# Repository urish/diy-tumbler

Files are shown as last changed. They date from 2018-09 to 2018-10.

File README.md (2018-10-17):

Do-It-Yourself Rock Tumbler
===========================

A simple Rock Tumbler I built from scratch in just a few hours.

For more information read the blog post: [Improvising Hardware: DiY Rotary Rock Tumbler](https://medium.com/@urish/improvising-hardware-diy-rotary-rock-tumbler-d3a1a1915ea9)

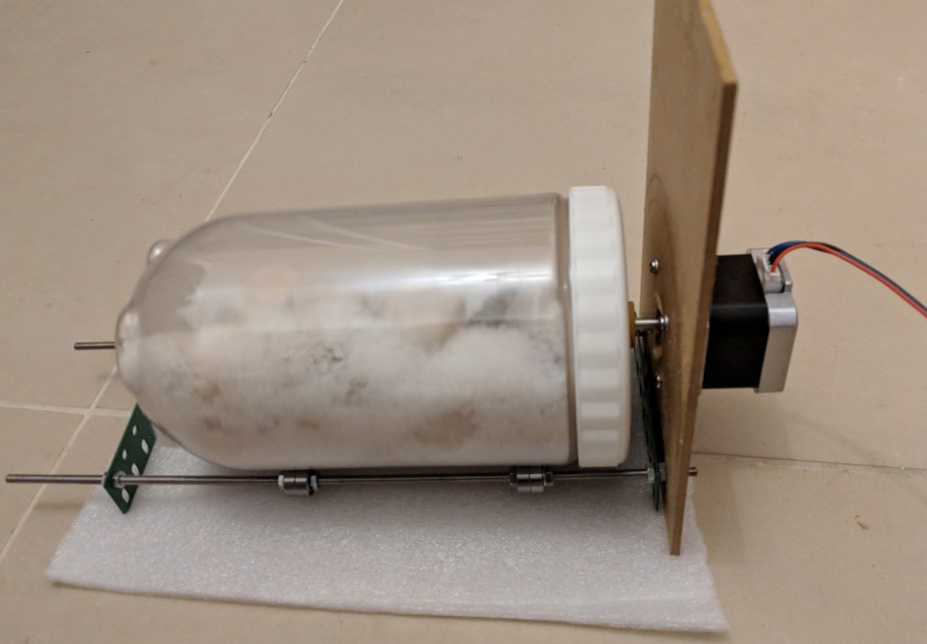
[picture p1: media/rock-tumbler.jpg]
DiY Rock Tumbler


## Bill of Materials

| Name | Quantity | Unit Price | Link | Comment |
|---| ---| --- | ---- | --- |
| Bipolar 1.7A 2.8V NEMA-17 Stepper Motor | 1 | $16.95 | [Pololu](https://www.pololu.com/product/2267) or [AliExpress](https://www.aliexpress.com/item/CE-certification-1pcs-4-lead-Nema17-Stepper-Motor-42-motor-Nema-17-motor-42BYGH-1-7A/32760823826.html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 )| |
| DRV8825 Motor Driver | 1 | $8.95 | [Pololu](https://www.pololu.com/product/2133) or [AliExpress](https://www.aliexpress.com/item/5pcs-lot-3D-Printer-Stepstick-Drv8825-Stepper-Motor-Driver-Reprap-4-PCB-Board-Free-shipping/32434801528.html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) |  |
| Pixl.js Espruino Board | 1 | $44.95 | [Espruino](https://shop.espruino.com/pixljs) or [AdaFruit](https://www.adafruit.com/product/3855) |  |
| KY-003 Hall Magnetic Sensor Module | 1 | $0.82 | [AliExpress](https://www.aliexpress.com/item/KY-003-Standard-Hall-Magnetic-Sensor-Module-Works-with-Arduino-Boards-for-Arduino/32693432353.html) | |
| A small magnet | 1 | | | |
| 28.8cm M4 Threaded Rod | 2 | - | | Different length possible |
| M4 Nut | 18 |  |  |  |
| M3x10 Screw | 12 | | | | 
| M3x8 Screw | 1 | | | |
| M3 Nut | 9 | | | |
| M3 Washer | 16 | | | |
| M2x16 Screw | 2 | | | |
| M2 Nut | 6 | | | |
| 624ZZ Bearing | 8 |  |  |  |
| Small Plastic Jar | 1 | | | |
| Small Plywood Board | 1 | | | |

You can replace the Pixl.js with a Arduino, though the built-in display make it really nice.

You also need to print 1 of each of these parts:
* [motor-mount.scad](hardware/parts/motor-mount.scad)
* [motor-hub.scad](hardware/parts/motor-hub.scad) - You may need to change the `diameter` variable to match the inner diameter of your Jar's cap (it can also be smaller)

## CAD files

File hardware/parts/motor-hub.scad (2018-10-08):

// Tumbling Machine - Motor Hub
// Copyright (C) 2018, Uri Shaked
// License: MIT

include <MCAD/units.scad>
use <../vitamins/nuts.scad>

diameter = 80;
totalHeight = 20;
hubHeight = 15;
hubDiameter = 22.5;
screwHeight = totalHeight - 5;
tolerance = 0.15;

$fn = 60;

module MotorHub() {
    difference() {
        union() {
            cylinder(h=totalHeight - hubHeight, r=diameter / 2);

            translate([0, 0, totalHeight - hubHeight])
            cylinder(r=hubDiameter / 2, h=hubHeight);
        }

        // motor shaft hole
        translate([0, 0, -epsilon])
        difference() {
            cylinder(r=2.5 + tolerance, h=totalHeight + 2*epsilon);

            translate([2.35 + tolerance, -5, 0])
            cube([10, 10, totalHeight+epsilon]);
        }

        // mounting holes
        for (angle = [0:360 / 8:360])
            rotate([0, 0, angle])
            translate([0, 30, 0])
            cylinder(r=M3 / 2 + tolerance, h=5 + epsilon);

        translate([0, 0, screwHeight]) {
            rotate([0, 90, 0])
            cylinder(h=hubDiameter/2 + epsilon, r = M3 / 2 + tolerance);

            translate([M3 / 2 + 3, 0, 0])
            rotate([90, 0, 90])
            NutM3Hole(2.4);
        }
    }
}

MotorHub();

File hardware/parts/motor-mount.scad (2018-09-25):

// Tumbling Machine - Motor Hub
// Copyright (C) 2018, Uri Shaked
// License: MIT

include <MCAD/units.scad>

$fn = 60;

mountWidth = 1.725 * inch;
mountThickness = 3;
pilotRadius = 0.433 * inch;
mountHoleDistance = 1.220 * inch;
mountHoleRadius = 1.5;
tolerance = 0.15;

module Nema17Mount() {
    difference() {
        translate([-mountWidth / 2, -mountWidth / 2, 0])
        cube([mountWidth, mountWidth, mountThickness]);

        translate([0,0,-0.05])
        cylinder(r=pilotRadius+tolerance, h=mountThickness + 0.1);

        // Motor mounting holes
        for (x=[0,1]) for (y=[0,1])
            mirror([x,y,0])
            translate([mountHoleDistance / 2, mountHoleDistance / 2,-0.05])
            cylinder(r=mountHoleRadius + tolerance,h = mountThickness + 0.1);
    }
}

Nema17Mount();

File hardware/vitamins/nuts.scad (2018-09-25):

include <MCAD/units.scad>
include <MCAD/materials.scad>

NutM3Radius = 3.2;

module NutM3(height = 2.4, tolerance = 0) {
    color(Steel)
    difference() {
        cylinder(h=height, r=NutM3Radius + tolerance, $fn = 6);

        translate([0, 0, -epsilon/2])
        cylinder(h=height+epsilon, r=1.5 + tolerance, $fn = 60);
    }
}

module NutM3Hole(height = 2.4, tolerance = 0.15, trap = true) {
    cylinder(h=height + tolerance, r=NutM3Radius + tolerance, $fn = 6);

    if (trap) {
        translate([-(NutM3Radius + tolerance), 0, 0])
        cube([(NutM3Radius + tolerance) * 2, (NutM3Radius + tolerance) * 2, height + tolerance]);
    }
}

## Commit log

2018-09-25 Improve motor hub
    [motor-hub.scad]
2018-09-25 docs: add BOM
2018-09-28 feat: add hall-effect revolution sensor
    - count and display revolutions
    - attempt slowing down and recovering if we detect loss of motion
2018-10-08 fix(hardware): make the motor hub thicker and more durable
    [motor-hub.scad]
2018-10-08 fix(firmware): add hall sensor debouncing
